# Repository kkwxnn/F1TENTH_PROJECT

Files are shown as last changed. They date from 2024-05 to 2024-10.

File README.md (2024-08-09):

# F1TENTH: Autonomous Ackermann Steering Mobile Robot

https://github.com/user-attachments/assets/e7468762-8f40-447a-a497-539dd0bba7ac

### Obstacle Avoidance
https://github.com/user-attachments/assets/739e911e-5323-4bcc-a1b8-9813c5cff750

## Table of Contents
1. [Hardware](#1-hardware)
   - [1.1 Chassis](#11-chassis)
   - [1.2 Laser Sensor](#12-laser-sensor)
   - [1.3 Sensors](#13-sensors)
   - [1.4 Microcontroller](#14-microcontroller)
   - [1.5 Processor](#15-processor)
   - [1.6 Motor](#16-motor)
   - [1.7 Motor Driver](#17-motor-driver)

2. [Electrical & Firmware](#2-electrical--firmware)
   - [2.1 Electrical Components](#21-electrical-components)
   - [2.2 F1TENTH PCB Schematic](#22-f1tenth-pcb-schematic)
   - [2.3 Firmware](#23-firmware)

3. [High-Level](#3-high-level)
   - [3.1 Docker Setup](#31-docker-setup)
     - [3.1.1 Prerequisites](#311-prerequisites)
     - [3.1.2 Services](#312-services)
     - [3.1.3 Usage](#313-usage)
   - [3.2 TF](#32-tf)
     - [3.2.1 Coordinate Frame Transformations](#321-coordinate-frame-transformations)
     - [3.2.2 Visualization](#322-visualization)
   - [3.3 Localization](#33-localization)
     - [3.3.1 Prepare Sensor for Localization](#331-prepare-sensor-for-localization)
     - [3.3.2 Wheel Odometry (Yawrate Odometry)](#332-wheel-odometry-yawrate-odometry)
   - [3.4 Mapping & Localization by Slam Toolbox](#34-mapping--localization-by-slam-toolbox)
     - [3.4.1 Creating Map](#341-creating-map)
     - [3.4.2 Creating Keepout Zone](#342-creating-keepout-zone)
   - [3.5 Navigation (Nav2)](#35-navigation-nav2)
     - [3.5.1 Costmap](#351-costmap)

4. [Usage](#4-usage)
   - [4.1 Run ydlidar_launch.py](#41-run-ydlidar_launchpy)
   - [4.2 Run robot_bridge.launch](#42-run-robot_bridgelaunch)
   - [4.3 Teleoperation](#43-teleoperation)
   - [4.4 Viapoint Generator](#44-viapoint-generator)
     - [4.4.1 Selecting Point from Map](#441-selecting-point-from-map)
       
## 1. Hardware
<div align="center">
  f1tenth pic
</div>

### 1.1. Chassis
- [TAMIYA 58720 1/10 R/C 4WD TT-02 Type-SRX Chassis Kit](https://www.tamiyausa.com/shop/110-4wd-shaft-drive-road-tt/rc-tt-02-type-srx-chassis-kit/)
  
### 1.2. Laser Sensor
- [YDLIDAR T-mini Pro](https://www.ydlidar.com/products/view/22.html)

### 1.3. Sensors
- 9-DOF Absolute Orientation IMU Fusion Breakout - BNO055
- [Optical Tracking Odometry Sensor - PAA5160E1](https://www.sparkfun.com/products/24904) (Optional)
  
### 1.4. Microcontroller
- [STM32L432KC](https://www.st.com/en/evaluation-tools/nucleo-l432kc.html)

### 1.5. Processor
- [Raspberry Pi 5 Computer with 8GB RAM](https://www.raspberrypi.com/products/raspberry-pi-5/)
  
### 1.6. Motor
- [TAMIYA 54612 BRUSHLESS MOTOR 02 Sensored 15.5T 2300KV](https://www.tamiya.com/english/products/54612/index.html) (For main drive motor)
- [MG996R Servo Tower Pro](https://www.towerpro.com.tw/product/mg996r/) (For steering motor)
  
### 1.7. Motor Driver
- [TAMIYA 45070 TBLE-04SR BRUSHLESS ELECTRONIC SPEED CONTROLLER](https://www.tamiya.com/english/products/45070/index.html)

 > [!TIP]
 > **High Point Setup**
 > 1. Press and hold down Set button. LED will light up in the order Red → Green → Orange → Red. Release the Set button when the LED is lit up Red, and it will start to flash Red.
 > 2. Apply full throttle and press Set button once. If procedure has been performed correctly, LED will start to double flash Red.
 > 3. Apply full brake and press Set button once. If procedure has been performed correctly, LED will turn off.
 > 
 > [Tamiya Brushless ESC 04SR Manual](https://www.tamiyausa.com/media/files/45070ml-1206-1b53.pdf)

## 2. Electrical & Firmware
### 2.1. Electrical Components
- Step down DC-DC 4.5-30V to 0.8-30V 12A
- HW-683 Module

### 2.2. F1TENTH PCB Schematic
View full PCB schematic in EasyEDA within [this link](https://u.easyeda.com/join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)

<div align="center">
  Schematic_F1TENTH_V4_2024-07-18
  PCB_F1TENTH_V4_2024-07-18
</div>

### 2.3. Firmware

Process for Setup Low-Level is within [this link](https://github.com/tanakon-apit/F1TENTH_PROJECT.git)

## 3. High-Level 

### 3.1. Docker Setup

Instructions for using the provided `docker-compose.yml` file to set up and run a micro-ROS agent and a ROS 2 desktop environment with VNC access.

#### 3.1.1. Prerequisites
- [Install Docker](https://www.digitalocean.com/community/tutorials/how-to-install-and-use-docker-on-ubuntu-22-04)
- Install Docker Compose

#### 3.1.2. Services
**1. micro_ros_agent** runs a micro-ROS agent that connects to a serial device.

- Image: `microros/micro-ros-agent:humble`
- Container Name: `micro-ros-agent`
- Network Mode: `host`
- Command: `serial --dev /dev/ttyACM0 --baudrate 2000000`
- Devices:
    - `/dev/ttyACM0:/dev/ttyACM0`
- Restart Policy: `unless-stopped`

**2. desktop_ros2** runs a ROS 2 desktop environment with VNC access, allowing you to interact with ROS 2 via a web browser. [Reference](https://github.com/Tiryoh/docker-ros2-desktop-vnc.git)

- Image: `kkwxnn/f1tenth-vnc:humble`
- Container Name: `desktop_ros2`
- Security Options:
    - `seccomp=unconfined`
- Shared Memory Size: `512m`
- IPC Mode: `host`
- Ports: `6080:80` (Maps port 6080 on your host to port 80 in the container)
- Volumes: 
    - `~/F1TENTH_PROJECT/ros2_ws:/f1tenth_ws:rw` (Mounts your local workspace to the container)
    - `/dev:/dev` (Mounts the host's /dev directory to the container)
- Devices:
    - `/dev/ttyUSB0:/dev/ttyUSB0`
- Restart Policy: `unless-stopped`

#### 3.1.3. Usage
**1. Start the Services**

To start the services defined in the docker-compose.yml file, navigate to the directory containing the file and run:

```
docker compose up 
```
**2. Connect Raspberry Pi via SSH**

- Finding IP Address of wlan0 (wifi)
```
ifconfig
```
- Connect Raspberry Pi your computer via SSH
```
ssh -L 6080:localhost:6080 [username]@[inet addr] 
```
For example: ```ssh -L 6080:localhost:6080 pi@192.168.0.152```

**3. Access the ROS 2 Desktop**

Open a web browser and navigate to http://127.0.0.1:6080/ to access the ROS 2 desktop environment via VNC.

**4. Reset the services**
```ctrl+c```

> [!WARNING]
> If you are unable to connect to the ROS 2 desktop via noVNC, follow these steps:
> 
> - Remove the container
> ```
> docker compose down
> ```
> 
> - Start the services again
> ```
> docker compose up 
> ```
> 
> - Reinstall the libraries and dependencies
> ```
> sudo apt update && rosdep update
> rosdep install --from-paths src
> ```

> [!TIP]
> To avoid the need to reinstall libraries and dependencies, you can push your Docker image to Docker Hub. Follow these steps to do.
> 
> Don't forget to **logout of ubuntu in docker** and **stop the docker** before pushing the image.
> ```
> docker stop [container_id_or_name]
> ```
> - Log in to Docker Hub
>
> ```
> docker login
> ```
> - Commit the container
> ```
> docker commit [container_id_or_name] your-username/your-repository:tag
> ```
>
> For example: ```docker commit 1a2b3c4d5e6f your-username/my-app:latest```
> 
> - Tag Your Docker Image
> ```
> docker tag your-image:tag your-username/your-repository:tag
> ```
> For example: ```docker tag my-app:latest your-username/my-app:latest```
>
> - Push the Image to Docker Hub
>
> ```
> docker push your-username/your-repository:tag
> ```
> For example: ```docker push your-username/my-app:latest```

> [!CAUTION]
> In the event that **Docker crashes** and **Docker images and containers disappear**, but **noVNC is still running**, you will need to repeat the `docker compose up` steps and clear the running noVNC instance by following these steps.
>
> - Identify Running noVNC 
> ```
> ps aux | grep localhost
> ```
> - Terminate the noVNC 
> ```
> sudo kill [Process IDs]
> ```
> For example: ```sudo kill 3322```
> - Restart Docker
> ```
> sudo service docker restart
> ```
> or
> ```
> sudo systemctl restart docker
> ```

### 3.2. TF

<div align="center">
  <img src="https://github.com/user-attachments/assets/e0d1709a-a66c-4ba6-8a19-d0308fb0f621" alt="Robot_Description" width="600">
</div>

#### 3.2.1. Coordinate Frame Transformations

#### 3.2.1.1. base_footprint -> **base_link**

- This transform represents the static relationship between the center of the robot base (`base_footprint`) and the floor (`base_link`).

#### 3.2.1.2. base_link -> **imu**

- This transform describes the static relationship between the robot's base (`base_link`) and the IMU (Inertial Measurement Unit) sensor (`imu`).

#### 3.2.1.3. base_link -> **left_wheel**

- This transform defines the revolute relationship between the robot's base (`base_link`) and the left wheel (`left_wheel`).

#### 3.2.1.4. base_link -> **right_wheel**

- This transform defines the revolute relationship between the robot's base (`base_link`) and the right wheel (`right_wheel`).

#### 3.2.1.5. base_link -> **steer**

- This transform defines the static relationship between the robot's base (`base_link`) and the lidar sensor (`steer`).

#### 3.2.1.6. imu -> **laser_frame**

- This transform defines the static relationship between imu (`imu`) and the lidar sensor (`laser_frame`). 

#### 3.2.1.7. base_link -> **optical_odom**

- This transform defines the static relationship between the robot's base (`base_link`) and the Optical Tracking Odometry Sensor (`optical_odom`).

#### 3.2.2. Visualization

#### 3.2.2.1. Launch Robot Description

- Run the following command to launch the robot's description

```
ros2 launch robot_bridge robot_bridge.launch.py 
```
#### 3.2.2.2. View Transformations

- Execute the following command to watch the relationships between the robot's transformations

```
ros2 run tf2_tools view_frames
```

This command opens a graphical interface displaying the relationships between different frames. The provided link shows an example image capturing these transformations:

<div align="center">
  <img src="https://github.com/user-attachments/assets/61efbc9a-44b0-4ba7-a626-1a6dac1811cc" alt="TF_frames" width="900">
</div>

### 3.3. Localization

#### 3.3.1. Prepare sensor for Localization

1) IMU Sensor

    - Calibration sensor

        To calibrate IMU sensor you need to use STM32Cubeide this calibration file is set up for `STM32L432KC` follow this link to low-level github (branch: CalibrateIMU) [[link]](https://github.com/tanakon-apit/F1TENTH_PROJECT/tree/CalibrateIMU)

        Open up the project `BNO_Calibrate` in STM32Cubeide.

        Monitor the `Calibrated` value in the debugger's live expressions to track calibration progress (Accel, Gyro, Magneto).

        - `Magnetometer`: Hold the sensor parallel to the ground and move it in a figure 8 pattern.
        - `Accelerometer`: Place the BNO055 sensor in these six stable positions for a few seconds each.
        - `Gyroscope`: Place the sensor in any stable position for a few seconds.

        After successful calibration, record the BNO offsets from the bno variable in the debugger's live expressions.

        Change branch from `CalibrateIMU` to `Main`, Within the project, navigate to the file `Mobile_Config.h` located in the `Config/inc` directory. Write the BNO offsets from recorded. Then upload code into `STM32L432KC`.

    - Find Offset & Covariance sensor

        - Using `Calibration Node` to find offset and covariance of imu.
            - Collect 10,000 sensor raw data && Save offset and covariance data in YAML file.

            ```
            ros2 run calibration_gen cal_node.py
            ```

            - Copy the information from `f1tenth_ws/install/calibration_gen/share/calibration_gen/config/sensor_calibration.yaml` and paste in `f1tenth_ws/src/calibration_gen/config/sensor_calibration.yaml` 

        - Eliminating noise at stationary state by cutting threshold this will be done by `mcu_bridge` Node.
        
            - `threshold`: 2 x std. x 3.89 (Modeling Noise as Normal Distribution)

    - Verification sensor 

        - Testing Absolute Orientation from imu

            Testing Condition:

            - Turn 90, 180, 360 Degree (R/L)
            - Turn Right then Left 90 Degree

            https://github.com/user-attachments/assets/508171c0-2647-4e11-aa7b-1ab644b267a2

        **The IMU will shift of ±6 degrees each time it completes a full 360-degree rotation.**

2) Laser Sensor 

**Install YDLIDAR ROS2 Driver** [Reference](https://github.com/YDLIDAR/ydlidar_ros2_driver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)

- Clone ydlidar_ros2_driver package for github in `src` folder

```
git clone https://github.com/YDLIDAR/ydlidar_ros2_driver.git 
```
- Clone YDLidar-SDK package for github in `src` folder

```
git clone https://github.com/YDLIDAR/YDLidar-SDK.git
```

- Build & Install [Reference](https://github.com/YDLIDAR/YDLidar-SDK/blob/master/doc/howto/how_to_build_and_install.md)

```
cd YDLidar-SDK
mkdir build
cd build
cmake ..
make
sudo make install
```

- Build ydlidar_ros2_driver package

```
cd [your_workspace]
colcon build --symlink-install
```

#### Usage: Laser Sensor

1. Connect LiDAR
```
ros2 launch ydlidar_ros2_driver ydlidar_launch.py
```

2. Visualization in RVIZ
```
ros2 launch ydlidar_ros2_driver ydlidar_launch_view.py 
```

<div align="center">
  <img src="https://github.com/user-attachments/assets/7b7f3aa2-0fd3-449e-af10-5252123fc776" alt="Lidar" width="550">
</div>

#### 3.3.2. Wheel Odometry (Yawrate Odometry)

**State Equation**

$$ 
\begin{bmatrix}
x_k \\
y_k \\
\theta_k \\
\beta_k \\
v_k
\end{bmatrix}
=\
\begin{bmatrix}
x_{k-1} + v_{k-1} \cdot \Delta t \cdot \cos(\beta_{k-1} + \theta_k) \\
y_{k-1} + v_{k-1} \cdot \Delta t \cdot \sin(\beta_{k-1} + \theta_k) \\
\theta_k \\
0 \\
\text{motor speed} \cdot \text{gear ratio} \cdot r
\end{bmatrix} 
$$

where:
- $x_k$ and $y_k$ are the vehicle's position coordinates at time step $k$.
- $\theta_k$ is the vehicle's orientation (heading angle) at time step $k$.
- $\beta_k$ is the vehicle's slip angle at time step $k$.
- $v_k$ is the vehicle's velocity at time step $k$.

**Verification**

A ceiling-mounted camera in the laboratory serves as a ground truth reference for verifying the yaw rate odometry calculations. These calculations are derived from data obtained from both a hall sensor and an IMU sensor.

<div align="center">
  <img src="https://github.com/user-attachments/assets/81ab683f-14e1-4523-b5d4-ec480f5cf7b3" alt="Camera" width="550">
</div>

#### Experiment 1: Circular Path for 5 Rounds at speed 0.5 m/s

| Position | Odometry Final Position (m) | Camera Final Position (m) | Final Position Error (m) | RMSE (m) |
|----------|-----------------------------|---------------------------|--------------------------|----------|
| X (Y axis of the car frame) | 3.71 | 3.59 | 0.12 | 0.16 |
| Y (X axis of the car frame) | 4.78 | 5.13 | -0.35 | 0.21 |

<div align="center">
  <img src="https://github.com/user-attachments/assets/8b13dcbc-7981-4dc6-95a7-168b0b864c3f" alt="Circular Path" width="550">
</div>

#### Experiment 2: Path Around the Object at speed 0.5 m/s

| Position | Odometry Final Position (m) | Camera Final Position (m) | Final Position Error (m) | RMSE (m) |
|----------|-----------------------------|---------------------------|--------------------------|----------|
| X (Y axis of the car frame) | 2.54 | 2.57 | -0.03 | 0.06 |
| Y (X axis of the car frame) | -1.20 | -1.00 | -0.20 | 0.11 |

<div align="center">
  <img src="https://github.com/user-attachments/assets/464721fc-f9a7-4065-8367-265360b34701" alt="Obj Path" width="550">
</div>

### 3.4. Mapping & Localization by Slam toolbox

#### 3.4.1. Creating Map

To create a map, run the following command:

```bash
ros2 launch robot_bridge caver_mapping.launch.py
```

Once RVIZ has fully loaded, you need to launch teleop to control the robot for creating map.

```bash
ros2 run teleop_twist_keyboard teleop_twist_keyboard
```

After you have created a map, you can save it using the following command:

```bash
ros2 launch robot_bridge vmegarover_save_map.launch.py
```

Two file will be saved where you ran the command in the folder maps. The `.pgm` file is the map image and the `.yaml` file is the map metadata.

You can change the map name by rename the `.pgm` and `.yaml` file. You also need to foward in to `.yaml` file and change the name to the same name as `.pgm` file

You can change the map name by renaming both the `.pgm` and `.yaml` files. Additionally, you need to open the `.yaml` file and modify the name within it to match the new `.pgm` file name.

Then, copy both files and paste into the `maps` folder located within the `src` folder.

To use a specific map, you'll need to modify the map file name within the Python launch script. 

Running the following command will open the Python launch script in Visual Studio Code:

```bash
code /src/robot_bridge/lauch/robot_bridge.launch.py
```
Finally, you will obtain a map similar to the one shown below.

<div align="center">
  Map
</div>

#### 3.4.2. Creating Keepout zone

To create a keepout zone, make a copy of both the `.pgm` and `.yaml` files and rename them to `keepout_<map_name>.pgm` and `keepout_<map_name>.yaml` respectively.

Open the `keepout_<map_name>.yaml` file and change the `image` parameter to `keepout_<map_name>.pgm`.

Using image editing software, such as GIMP, draw the area you want to keepout in black. The rest of the image is left as is.

<div align="center">
  Keepout
</div>

### 3.5. Navigation (Nav2)

#### 3.5.1. Costmap

Environment representation used for planning and control. Combines sensor data (depth, AI, semantics) into a grid, assigning costs to cells. Higher costs indicate obstacles or risky areas. [Reference](https://docs.nav2.org/configuration/packages/configuring-costmaps.html)

-  Critical Costmap2D ROS Parameters 
    - `Footprint`

        polygon updated over time due to change of robot's state (base_footprint). If this parameter is set, `isPathValid` will do full collision checking.
        - `Robot_radius`: If footprint coordinates not provided. If this parameter is set, `isPathValid` will do circular collision checking.
    - `plugin`: 
        - `StaticLayer`: 
        
            Static obstacles on the planning space.
            - `footprint_clearing_enabled`: Clear any occupied cells under robot footprint.

        - `ObstacleLayer`:

            Costmap layeruses that use 2D raycasting for 2D lidars, depth, or other sensors. Manages the planning space by the parameters specified
            
            - `obstacle_max_range` / `obstacle_min_range`:
            Maximum, Minimum range to mark obstacles in costmap.
            - `raytrace_max_range` / `raytrace_min_range`
        - `InflationLayer`:

            This layer places an exponential decay functions around obstacles to increase cost to traverse near collision.

            - `inflation_radius`:
            Radius to inflate costmap around lethal obstacles.
            - `cost_scaling_factor`: Exponential decay factor across inflation radius.

-  Costmap2D ROS Parameters tunning guide

    - `Footprint`: For precise navigation in tight spaces, use a detailed robot footprint. In open areas, a simple `Robot_radius` can optimize performance (Collision detection computation time).

    - `obstacle_max_range`-`obstacle_min_range` / `raytrace_max_range`-`raytrace_min_range`: A longer sensor range enhances obstacle detection, improving path planning and collision avoidance. Conversely, a shorter range can expedite computation but limits obstacle awareness.

    - Increasing both `inflation_radius` and `cost_scaling_factor` amplifies the cost area around obstacles. To achieve a stronger cost effect, prioritize increasing `cost_scaling_factor` first (more `cost_scaling_factor` will decrease cost area).

<div align="center">
  costmap_lowcost
  costmap_highcost
  
  *`inflation_radius`: low [0.275], high [2.0]*
  
  *`cost_scaling_factor`: low [15.0], high [16.5]*
</div>

 - Example of the nav2 configuration can be found at the following [here](https://github.com/kkwxnn/F1TENTH_PROJECT/blob/humble/f1tenth_ws/src/robot_bridge/config/navigation_param.yaml).

#### 3.5.2. Planner

`Smac Hybrid-A* Planner`

Creates various A* planners for different robots (cars, legged). Supports Hybrid-A* for complex maneuvers (kinematically feasible and support reversing). [Reference](https://docs.nav2.org/configuration/packages/configuring-smac-planner.html)

-  Critical Planner ROS Parameters

    - `allow_unknown`: Allow traversing/search in unknown space.
    - `motion_model_for_search`: Motion model (`Dubin`, `Redds-Shepp`). 
    - `minimum_turning_radius`: Minimum turning radius in meters of vehicle.
    - `reverse_penalty`: Heuristic penalty to apply to SE2 node if searching in reverse direction. Only used in `REEDS_SHEPP` motion model.
    - `non_straight_penalty`: Heuristic penalty to apply to SE2 node if searching in non-straight direction.
    - `cost_penalty`: Heuristic penalty to apply to SE2 node for cost at pose. Allows Hybrid-A* to be cost aware.

 - Example of the nav2 configuration can be found at the following [here](https://github.com/kkwxnn/F1TENTH_PROJECT/blob/humble/f1tenth_ws/src/robot_bridge/config/navigation_param.yaml).

 - Planner ROS Parameters tunning guide: 

    - Reccomend `Dubin` if the robot has not recommend to reverse.

    - Using the exact `minimum_turning_radius` aids robot to follow, while a slightly reduced value can smooth path planning.
    <div align="center">
      low_curvature
      high_curvature
      
      *`minimum_turning_radius`: low [0.73], high [1.20]*
    </div>

    - Increasing the `non_straight_penalty` heuristic promotes straighter paths in path planning.

    <div align="center">
      Non_straight_penalty
      straight_penalty
      
      *`non_straight_penalty`: low [1.2], high [2.0]*
    </div>

    - A higher `cost_penalty` incentivizes the planner to avoid high-cost regions, typically obstacles.

#### 3.5.3. Controller

`Regulated Pure Pursuit`

Adaptive speed based on path curvature for safer industrial robot navigation. Prevents overshoot in corners. [Reference](https://docs.nav2.org/configuration/packages/configuring-regulated-pp.html)

If you use the Regulated Pure Pursuit Controller algorithm or software from this repository, please cite this work in your papers:
Macenski, S. Singh, F. Martin, J. Gines, [Regulated Pure Pursuit for Robot Path Tracking](https://arxiv.org/abs/2305.20026). Autonomous Robots, 2023.

- Controller ROS Parameters tunning

    - `desired_linear_vel`: The desired maximum linear velocity (m/s) to use.

    - `use_velocity_scaled_lookahead_dist` is `false`.
        - `lookahead_dist`: The lookahead distance (m) to use to find the lookahead point when 

    - `use_velocity_scaled_lookahead_dist` is `true`.
        - `min_lookahead_dist` / `max_lookahead_dist`: The minimum / maximum lookahead distance (m) threshold when 

        - `lookahead_time`: The time (s) to project the velocity. Also known as the lookahead gain.

    - `use_cost_regulated_linear_velocity_scaling`: Whether to use the regulated features for proximity to obstacles (e.g. slow in close proximity to obstacles).

    - `use_regulated_linear_velocity_scaling`: use the regulated features for path curvature (e.g. slow on high curvature paths).

        - `regulated_linear_scaling_min_radius`: The turning radius (m) for which the regulation features are triggered.

    - `regulated_linear_scaling_min_speed`: To ensure process is still achievable even in high cost spaces with high curvature.

    - `use_fixed_curvature_lookahead`: Use a fixed lookahead distance to compute curvature from.

        - `curvature_lookahead_dist`: Distance to look ahead on the path to detect curvature.

- Controller ROS Parameters tunning guide:

    - `Regulated Pure Pursuit` enhances curve following by adjusting speed through the `regulated_linear_scaling_min_radius` parameter. Higher values reduce speed on tighter curves.

    - Enabling `use_cost_regulated_linear_velocity_scaling` prioritizes obstacle avoidance by reducing speed in high-cost areas.

    - If the area the robot need to traverse high-cost areas, increasing `regulated_linear_scaling_min_speed` enables the robot to traverse by maintaining a minimum velocity.

 - Example of the nav2 configuration can be found at the following [here](https://github.com/kkwxnn/F1TENTH_PROJECT/blob/humble/f1tenth_ws/src/robot_bridge/config/navigation_param.yaml).

 #### 3.5.4. AMCL

 AMCL implements the server for taking a static map and localizing the robot within it using an Adaptive Monte-Carlo Localizer. [Reference](https://docs.nav2.org/configuration/packages/configuring-amcl.html)

 -  Critical AMCL ROS Parameters 

    - Odometry
        - `alpha1`: Expected process noise in odometry’s rotation estimate from rotation.
        - `alpha2`: Expected process noise in odometry’s rotation estimate from translation.
        - `alpha3`: Expected process noise in odometry’s translation estimate from translation.
        - `alpha4`: Expected process noise in odometry’s translation estimate from rotation.
        - `pf_err`: Particle Filter population error.
        - `pf_z`: Particle filter population density. 2.33 is the 99% percentile.
    - Laser (Lidar)
        - `laser_likelihood_max_dist`: Maximum distance to do obstacle inflation on map, for use in likelihood_field model.
        - `sigma_hit`: Standard deviation for Gaussian model used in z_hit part of the model.
        - `z_hit` / `z_rand`: Mixture weight for z_hit part of model, sum of all used z weight must be 1.

- AMCL ROS Parameters tunning guide:

    - Our odometry model is more stable than the laser scan (lidar) data.

    - For a reliable odometry model, reduce expected process noise (`alpha`) and `pf_er`r, while increasing `pf_z`.

    - For unreliable lidar data, increase `z_hit` and `sigma_hit` to incoporate higher measurement noise.

 - Example of the nav2 configuration can be found at the following [here](https://github.com/kkwxnn/F1TENTH_PROJECT/blob/humble/f1tenth_ws/src/robot_bridge/config/navigation_param.yaml).

Parameters prioritize `odometry` over `lidar`.
```
lazer_z_hit = 0.9
laser_sigma_hit = 0.1
laser_z_rand = 0.5
laser_likelihood_max_dist = 4.0
kld_err = 0.01
kld_z = 0.99
odom_alpha1 = 0.005
odom_alpha2 = 0.005
odom_alpha3 = 0.005
odom_alpha4 = 0.005
```
https://github.com/user-attachments/assets/a85da535-ef96-4c38-8924-c9d862924488

Parameters prioritize `lidar` over `odometry`.
```
lazer_z_hit = 0.5
laser_sigma_hit = 0.2
laser_z_rand = 0.5
laser_likelihood_max_dist = 2.0
kld_err = 0.1
kld_z = 0.5
odom_alpha1 = 0.004
odom_alpha2 = 0.04
odom_alpha3 = 0.008
odom_alpha4 = 0.025
```

https://github.com/user-attachments/assets/7fe0a6d9-28dd-49fd-9026-d1f11126844d

 **Verification**

 #### Experiment 1: Path Around the Object at Speed 0.5 m/s

| Position | Camera Last Position (m) | TF Last Position (m) | Error Odom Last Position (m) | Error AMCL Last Position (m) | Error TF Last Position (m) | RMSE TF (m) |
|---|---|---|---|---|---|---|
| X (Y axis of the car frame) | 2.57 | 2.62 | -0.03 | 0.10 | 0.05 | 0.11 |
| Y (X axis of the car frame) | -1.00 | -1.05 | -0.20 | 0.05 | -0.05 | 0.14 |

<div align="center">
  amcl_tune0.5
</div>

#### Experiment 2: Path Around the Object at Speed 2.0 m/s

| Position | Camera Last Position (m) | TF Last Position (m) | Error Odom Last Position (m) | Error AMCL Last Position (m) | Error TF Last Position (m) | RMSE TF (m) |
|---|---|---|---|---|---|---|
| X (Y axis of the car frame) | 2.53 | 2.55 | -0.19 | 0.00 | 0.01 | 0.40 |
| Y (X axis of the car frame) | 0.69 | 0.66 | -0.18 | 0.02 | -0.03 | 0.47 |

<div align="center">
  amcl_tune2.0
</div>

## 4. Usage

To run the robot, you should first connect to Docker and then run the following terminal commands.

### 4.1. Run ydlidar_launch.py
```
ros2 launch ydlidar_ros2_driver ydlidar_launch.py 
```

### 4.2. Run robot_bridge.launch 
```
ros2 launch robot_bridge robot_bridge.launch.py
```

### 4.3. Teleoperation
```
ros2 run teleop_twist_keyboard teleop_twist_keyboard
```
[Reference](https://index.ros.org/r/teleop_twist_keyboard/)
```
This node takes keypresses from the keyboard and publishes them as Twist
messages. It works best with a US keyboard layout.
---------------------------
Moving around:
   u    i    o
   j    k    l
   m    ,    .

For Holonomic mode (strafing), hold down the shift key:
---------------------------
   U    I    O
   J    K    L
   M    <    >

t : up (+z)
b : down (-z)

anything else : stop

q/z : increase/decrease max speeds by 10%
w/x : increase/decrease only linear speed by 10%
e/c : increase/decrease only angular speed by 10%

CTRL-C to quit
```
### 4.4. viapoint generator

#### 4.4.1. Selecting point from Map

After lauch robot_bridge.launch.py

```
ros2 topic echo /clicked_point 
```

Click the `Publish Point` button, then select the desired goal point. 

Edit the goal point by modifying the `self.current_goal_pose` value (in [x, y, yaw] format) within the `navigation_param.yaml` file located in the `src/robot_bridge/config` directory.

For example: `self.current_goal_pose` = [[3.6, 0.0, np.deg2rad(0)]]

```
code src/robot_bridge/config/navigation_param.yaml
```

> [!WARNING]
> If your next goal point doesn't generate (Feedback: Reached), consider relocating it or increasing the error threshold. Path planning difficulties might be causing the issue.

After defining all goal points you can execute the Python script from Visual Studio Code or run it as a command below:

```
ros2 run robot_bridge via_points_generator.py
```

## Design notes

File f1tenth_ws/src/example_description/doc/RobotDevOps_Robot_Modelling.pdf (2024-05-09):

# NOTICE OF CONFIDENTIALITY AND USE RESTRICTIONS

This PowerPoint presentation, including all of its contents, is the intellectual property of Pi Thanacha Choopojcharoen. It has been exclusively designed and created for the "RobotDevOps" class.
Authorized Users:
If you are currently enrolled in or have previously taken the "RobotDevOps" class and are in possession of this presentation, you acknowledge and agree to the following:
a) This presentation is provided to you solely for your personal reference and educational use related to the "RobotDevOps" class.
b) You do not have the right to reproduce, distribute, share, or disseminate this presentation, in whole or in part, to any third parties, especially those who have not registered for the "RobotDevOps" class, unless explicitly authorized by Pi Thanacha Choopojcharoen.
c) Any unauthorized use or distribution of this presentation will result in legal action and potential academic sanctions. Unauthorized Possession:
a) If you have come into possession of this presentation but have not registered for the "RobotDevOps" class: You must delete this presentation immediately.
b) You do not have any rights to view, use, copy, or distribute this presentation.
c) Any unauthorized retention or use will result in legal action.

Your respect for intellectual property rights ensures a fair academic and professional environment for all. Violation of these terms is a breach of trust and may have serious legal and academic consequences.

For FRA502 only

# RBE502: RobotDevOps

# Robot Modelling

by

## Pi Thanacha Choopojcharoen

Agenda - purpose - interface - coordinate frame - visualization - URDF - XACRO - Frame prefix

# Exercise

# Exercise

Exercise

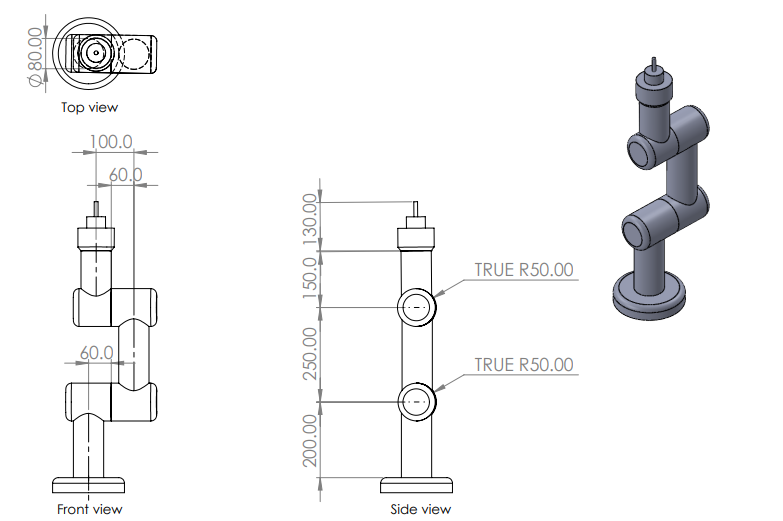
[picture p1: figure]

# Exercise

Exercise

F1

Fbase

F2

F3

Fe

# Exercise

Exercise

F1

Fbase

F2

F3

Fe

Create the robot “kinematics” model and visualize it in rviz.
[Optional] It should take namespace as well.

# Example Repo- Branch: robot-modelling-exercise

## https://github.com/kittinook/FRA501/tree/robot-modelling-exercise

## Download & add “example_description” to the “src” directory of your

workspace. Then build these packages.

## Follow the instruction on README.md

Exercise

# Existing Packages

# Type of ROS2 Packages

10 Existing Packages

Binary Package | Source Package

# Type of ROS2 Packages

11 Existing Packages

Binary Package | Source Package

Installing aruco_msgs package:

>> sudo apt install ros-humble-aruco-msgs

All underscore must be changed to hyphen.

# Type of ROS2 Packages

12 Existing Packages

Binary Package | Source Package

Installing aruco_msgs package:

>> sudo apt install ros-humble-aruco-msgs

Clone the package to “src” folder of the workspace and treat it as any other custom package.

# What binary packages are available?

13 Existing Packages

https://index.ros.org/packages

>> apt search ros-humble-

# Available & Installed Packages

14 Existing Packages

Check package’s existence in the binary package index

>> apt list ros-humble-aruco*

Check installed packages on the computer

>> apt list --installed ros-humble-aruco*

“aruco*” means any package with the name starts with “aruco” and ends with anything.

# Package Dependencies

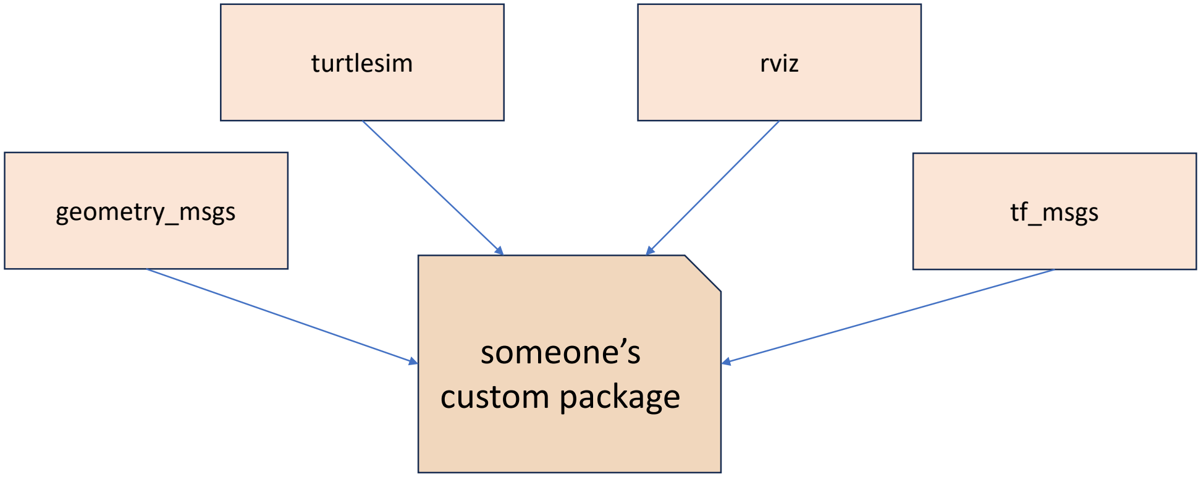
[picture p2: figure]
someone’s custom package; geometry_msgs; turtlesim; rviz; tf_msgs

15 Existing Packages

# Package Dependencies

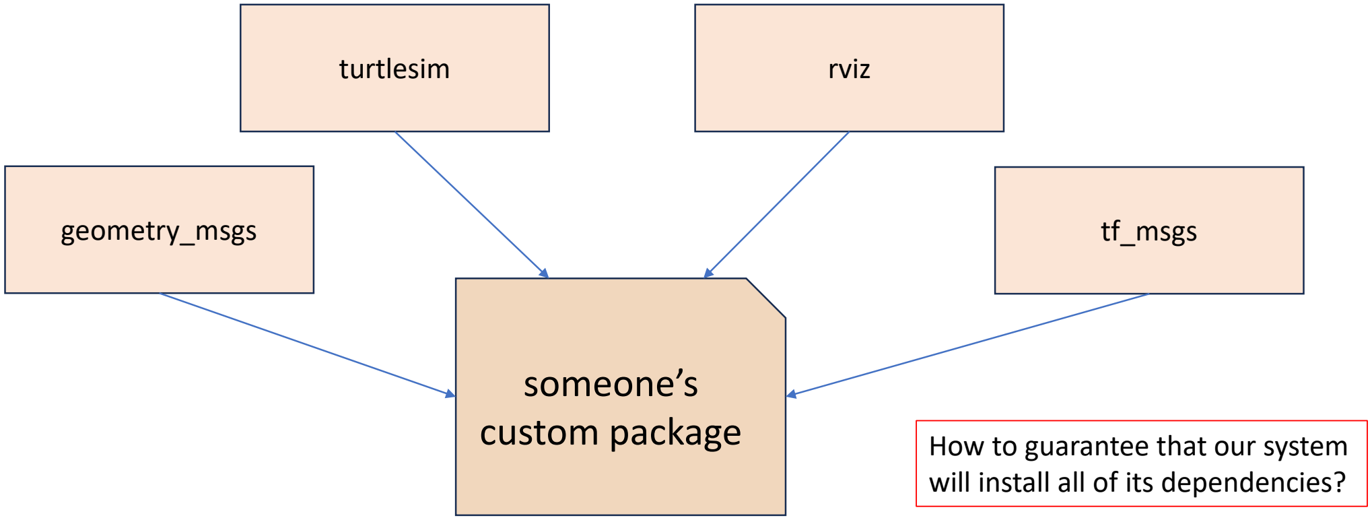
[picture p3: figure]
someone’s custom package; geometry_msgs; turtlesim; rviz; tf_msgs; How to guarantee that our system will install all of its dependencies?

16 Existing Packages

# Package Dependencies

17 Existing Packages

# Package Dependencies

18 Existing Packages

# 80 % Accurate

# Setting Package Dependencies

19 Existing Packages

In “package.xml” of your custom package, add <depends> tags for each binary package.

<depend> geometry_msgs </depend>
<depend> turtlesim </depend>

https://docs.ros.org/en/humble/Tutorials/Intermediate/Rosdep.html

# Installing Package Dependencies

20 Existing Packages

Run the following command to install the dependency of everything in the “src” folder of your workspace.

>> rosdep install --from-paths [path to your src]/src -y --ignore-src

https://docs.ros.org/en/humble/Tutorials/Intermediate/Rosdep.html

# Today’s packages

21 Existing Packages

## Additional packages:

## ros-humble-tf2-tools ros-humble-xacro ros-humble-joint-state-publisher-gui

## >> sudo apt install ros-humble-[package name]

https://docs.ros.org/en/humble/Tutorials/Intermediate/Rosdep.html

# Robot Modelling

# Questions regarding “Robot Modelling”

23 Robot Modelling

## What is “Robot Modelling”? Why do we need “Robot Modelling”? When do we need “Robot Modelling”? Who models robots? Who need “Robot Modelling”? Where do we do “Robot Modelling”? How do we model robots?

# What is Robot Modelling?

Robot Modelling

# What is Robot Modelling?

Robot Modelling

# What is Robot Modelling?

Concepts

Vague, Uncertain,
Some ideas

Robot Modelling

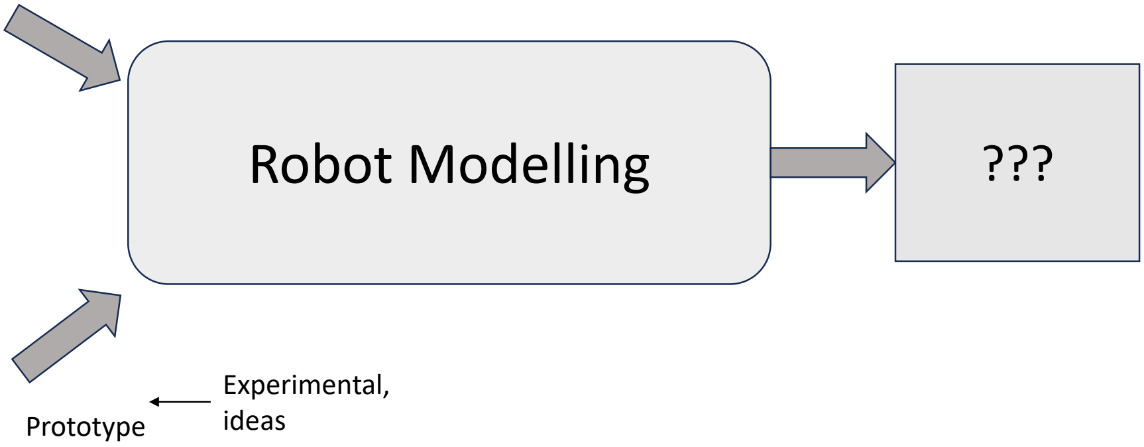
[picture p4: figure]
Robot Modelling; Prototype; Experimental, ideas

# What is Robot Modelling?

Concepts

Robot Modelling

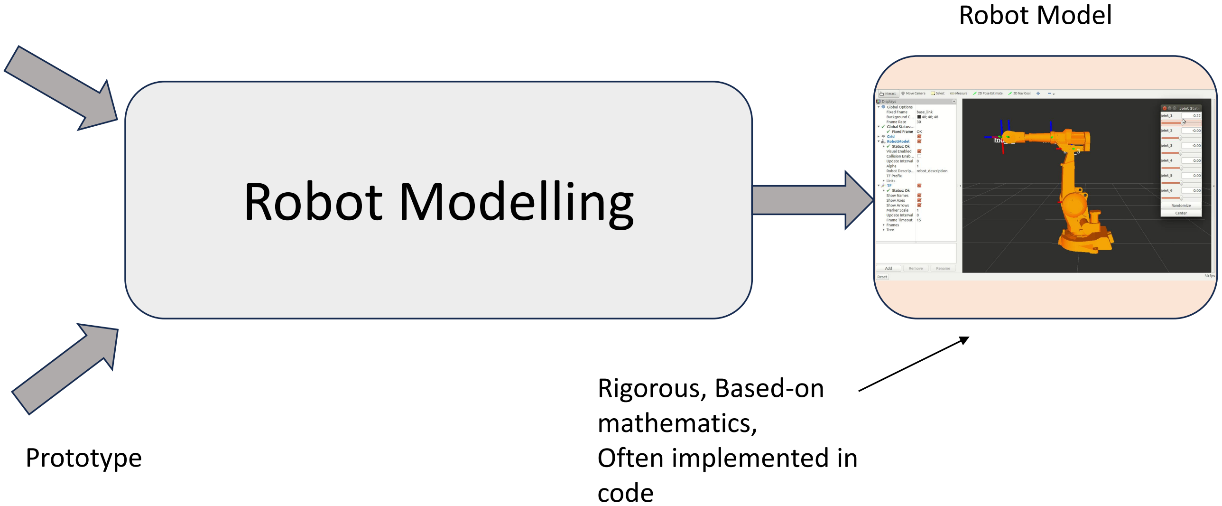
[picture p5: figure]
Robot Modelling; Prototype; Robot Model; Rigorous, Based-on mathematics, Often implemented in code

# What are robot models? And why do we need them ?

Robot Modelling

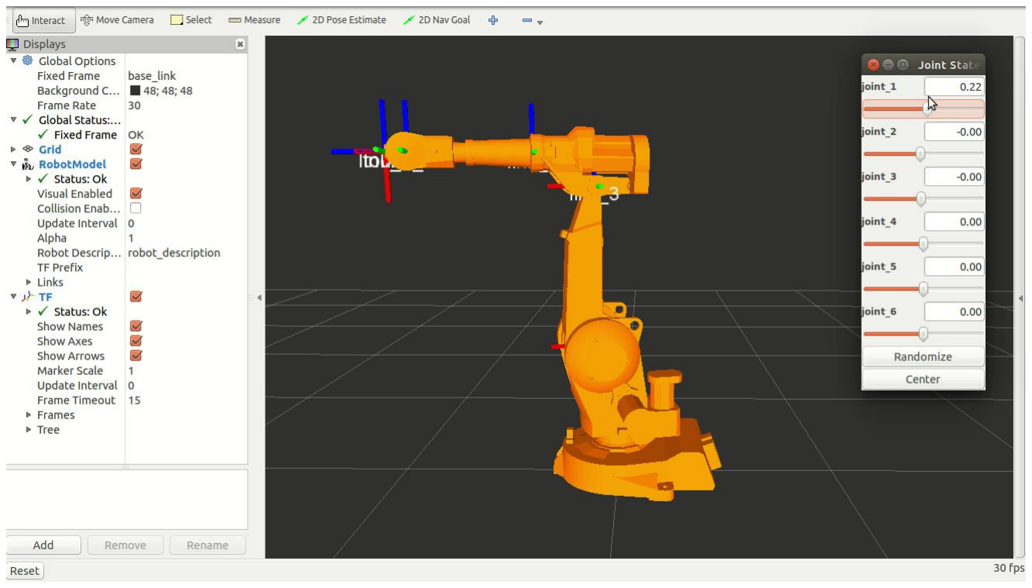
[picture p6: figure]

# What is it that the model can do, but the concept or a prototype cannot?

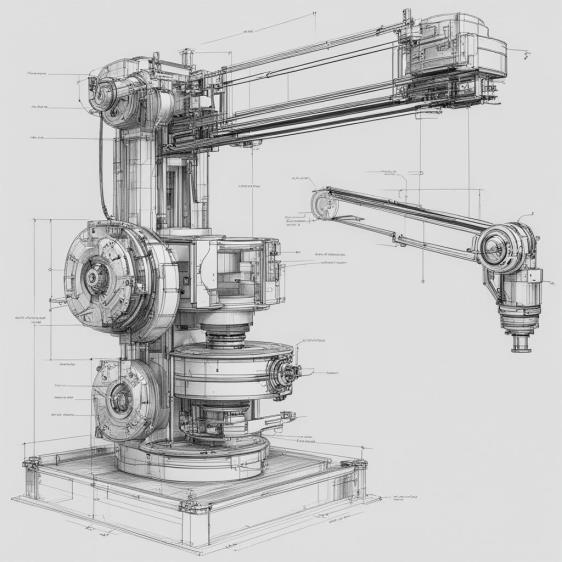
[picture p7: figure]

Robot Modelling

# Why?

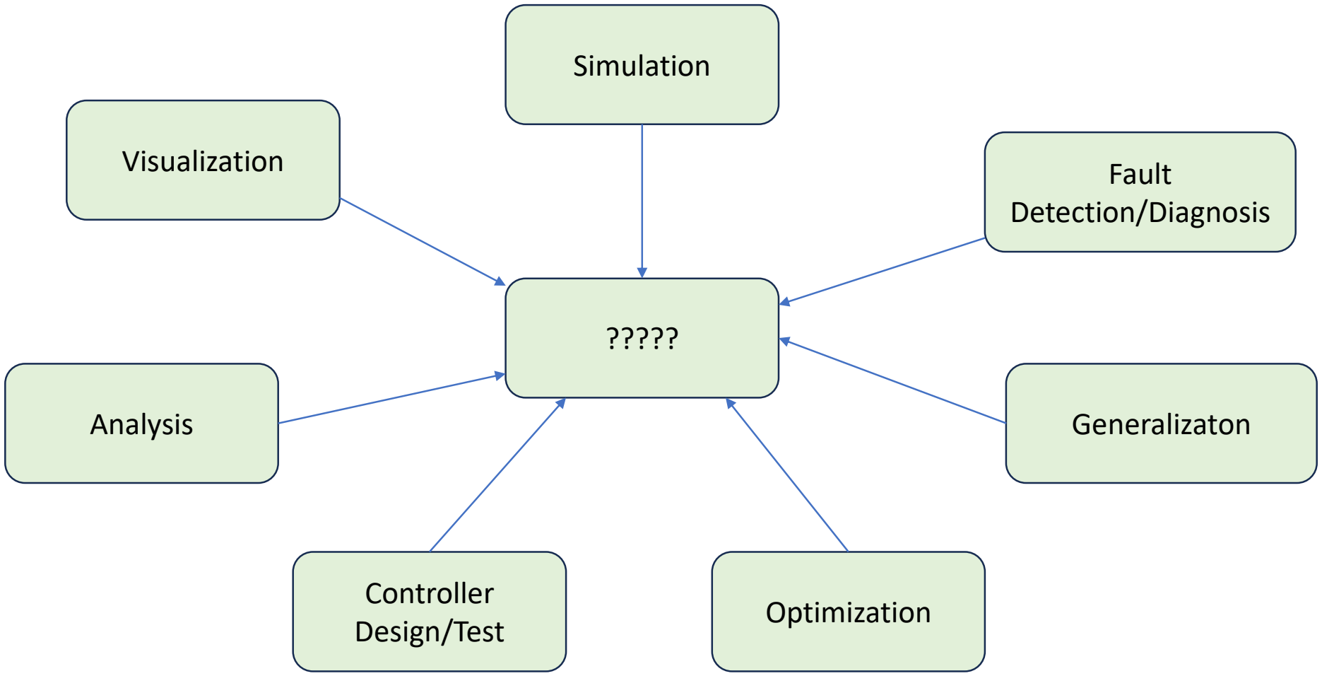
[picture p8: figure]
Simulation; Visualization; Analysis; Controller; Design/Test; Optimization; Fault Detection/Diagnosis; Generalizaton

Robot Modelling

# Why?

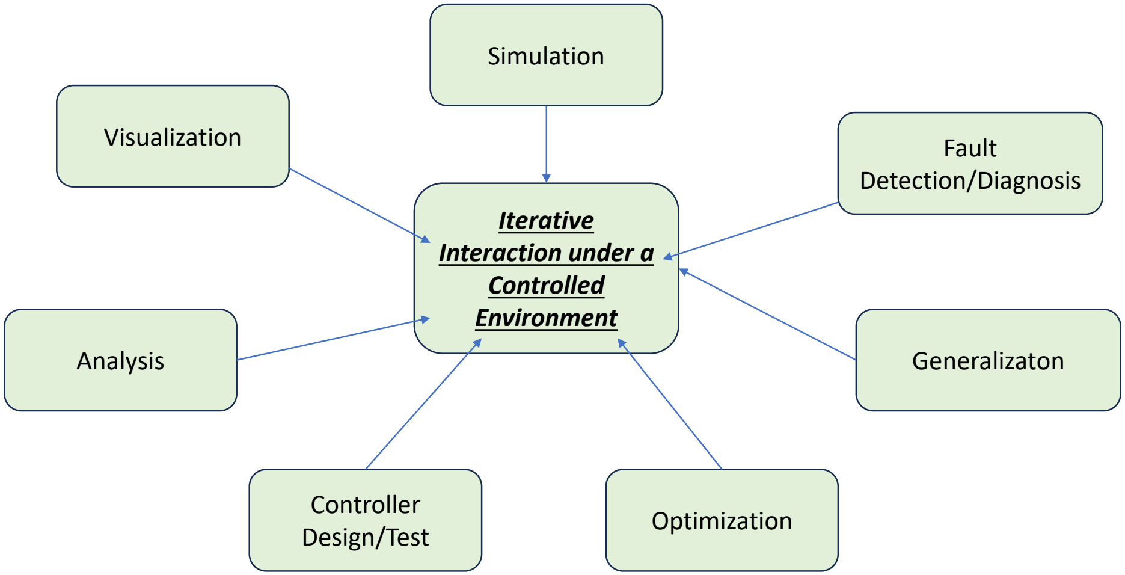
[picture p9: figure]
Simulation; Visualization; Analysis; Controller; Design/Test; Optimization; Fault Detection/Diagnosis; Generalizaton; Iterative Interaction under a Controlled Environment

Robot Modelling

## When do we need to “Robot Modelling”?

Robot Modelling

When the user requires “Iterative Interaction under a Controlled Environment”.

# What is a “robot model”?

Robot Modelling

We must identify these interfaces before “shaping” our robot model.

# Interface for a Robot Model

# What do you want from the model?

Robot Modelling

# What do you want from the “interaction”?

Robot Modelling

- Observe the position of the end-effector - Observe how fast something is going - Measure the distance travelled - Measure the actuated torque at certain revolute joints - Measure reaction force between the contact point and the ground - Obtain an ideal sensor measurement from the model - Observe any collision between the robot and the obstacle

# What do you want from the “interaction”?

Robot Modelling

- Observe the position of the end-effector - Observe how fast something is going - Measure the distance travelled - Measure the actuated torque at certain revolute joints - Measure reaction force between the contact point and the ground - Obtain an ideal sensor measurement from the model - Observe any collision between the robot and the obstacle

# Physical Quantities/Variables

Robot Modelling

Motion | Wrench
- Pose
- Joint
- Orientation
- Position
- Velocity
- Joint
- Angular
- Linear
- Acceleration
- Joint
- Angular
- Linear
- Actuator Effort
- Moment
- Force

# What can you do to the “interaction”?

Robot Modelling

# What can you do to the “interaction”?

Robot Modelling

## - Jog each joint separately - Move the end-effector in cartesian space - Actuate torque at the joint’s level - Give a motion trajectory for the robot to follow - Given an external force to the chassis of a robot

# Giving & Getting Physical Quantities

Robot Modelling

Robot Modelling

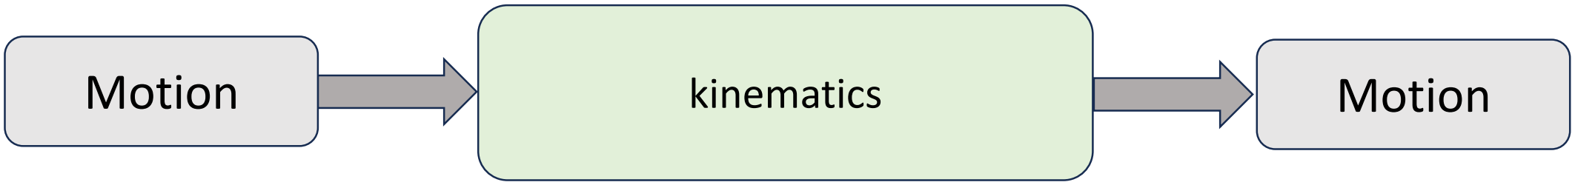
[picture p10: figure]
Motion; kinematics

Robot Modelling

Kinematics: study of motion regardless of force

Robot Modelling

in joint space | in taskspace

Robot Modelling

in joint space | in taskspace

Robot Modelling

in joint space | in taskspace

Robot Modelling

in taskspace | in joint space

Robot Modelling

Robot Modelling

Robot Modelling

Robot Modelling

Robot Modelling

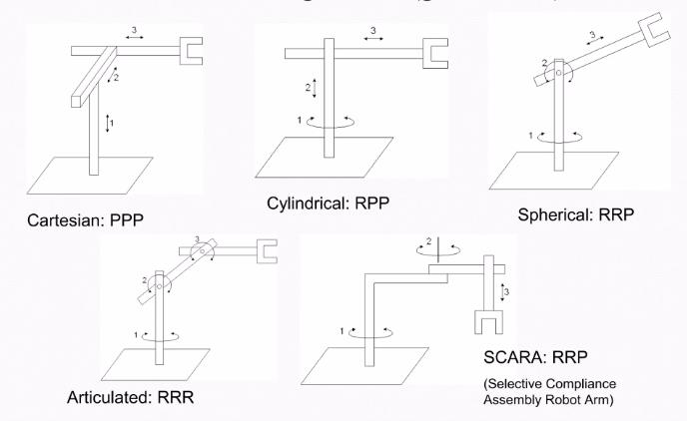
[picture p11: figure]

## Kinematics Model

## Dynamics Model

# Robot Model: Kinematics & Dynamics

# Rigid Body &Coordinate Frame

## - To describe the physical properties of

## a rigid body, one needs at least one reference “coordinate frame” - This frame is known as the “body-

attached” frame or “body” frame.

## Q.) Does a coordinate frame need to have a body?

Robot Modelling

# Tracking a pose

We can track a pose of an entire body by only tracking a pose of its body frame.

Robot Modelling

# Coordinate Frame

## Coordinate Frame consists of - an origin that describes its position - 3 orthogonal axes that describes its orientation

Fℬ

Robot Modelling

# Global Simulation Frame

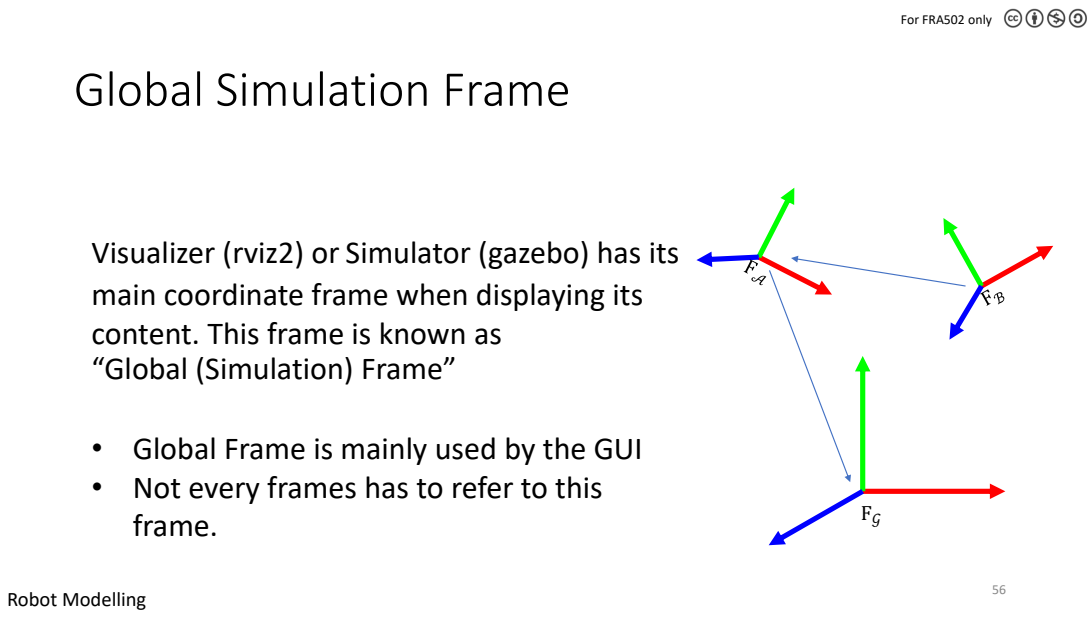
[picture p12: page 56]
frame.; Robot Modelling

Visualizer (rviz2) or Simulator (gazebo) has its
main coordinate frame when displaying its
content. This frame is known as
“Global (Simulation) Frame”

• Global Frame is mainly used by the GUI
• Not every frames has to refer to this

# Transform

# Transform

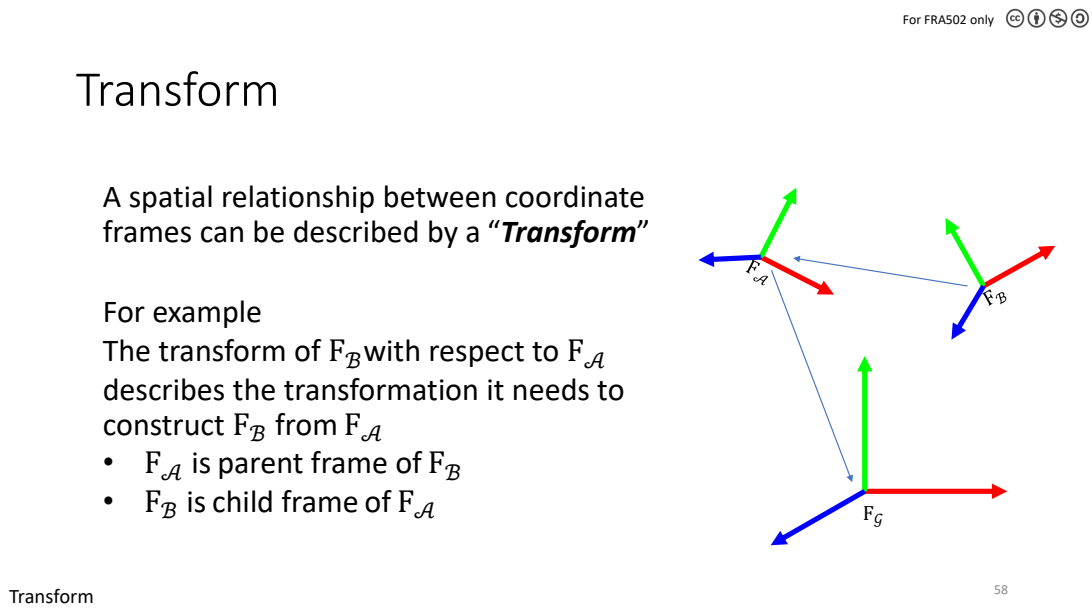
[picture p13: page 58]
Transform

A spatial relationship between coordinate
frames can be described by a “Transform”

For example
The transform of Fℬwith respect to FA
describes the transformation it needs to
construct Fℬ from FA
• FA is parent frame of Fℬ
• Fℬ is child frame of FA

# Components of a Transform

## Rotation :3 DOF - Quaternion: q = qx, qy, qz

, qw

## Translation : 3 DOF - Vector3 : p = px, py, pz

Transform

# Keeping track of Transforms

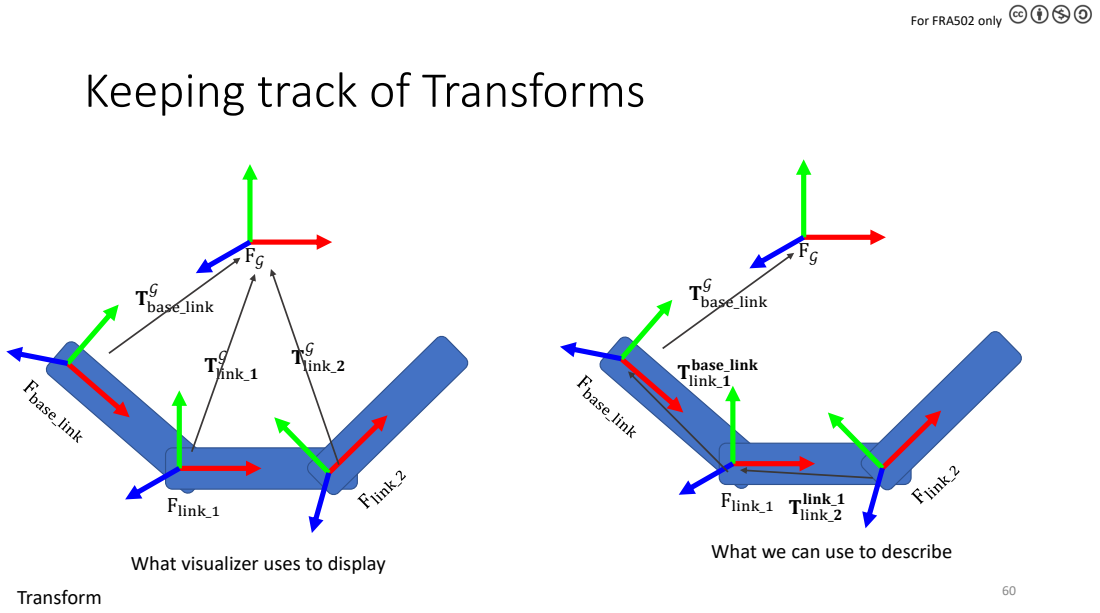
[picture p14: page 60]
60 Transform; Flink_1; Tbase_link; Tlink_1; Tlink_2; base_link; link_1

What we can use to describe What visualizer uses to display

tf2

We don’t have to create a system that track all coordinate frames. ROS2 already has a very special topic for this feature, which is known as tf2 .

ROS2 uses a topic “/tf”, which is an array of TransformStamped , to keep track of an entire tree (or multiple trees) in the system.

Transform

# tf2 in reality: tf & tf_static

To optimize the performance, the system usually has 2 Transform trees:
- /tf : this regular tf is used to describe “varying” transforms such as a pose of a mobile robot w.r.t. a fixed landmark.
- /tf_static: this tf is used to describe any fixed transforms such as the pose between lidar link and its attached chassis.

Transform

# tf2 in reality: tf & tf_static

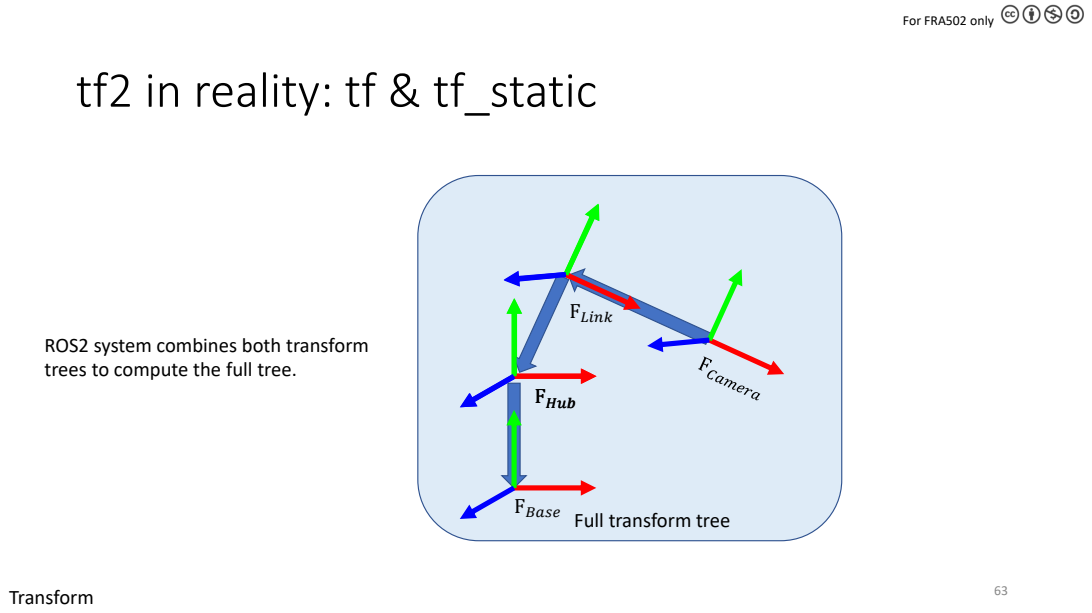
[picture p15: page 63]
Transform; FHub; FLink

ROS2 system combines both transform
trees to compute the full tree.

FBase
Full transform tree

# tf2 in reality: tf & tf_static

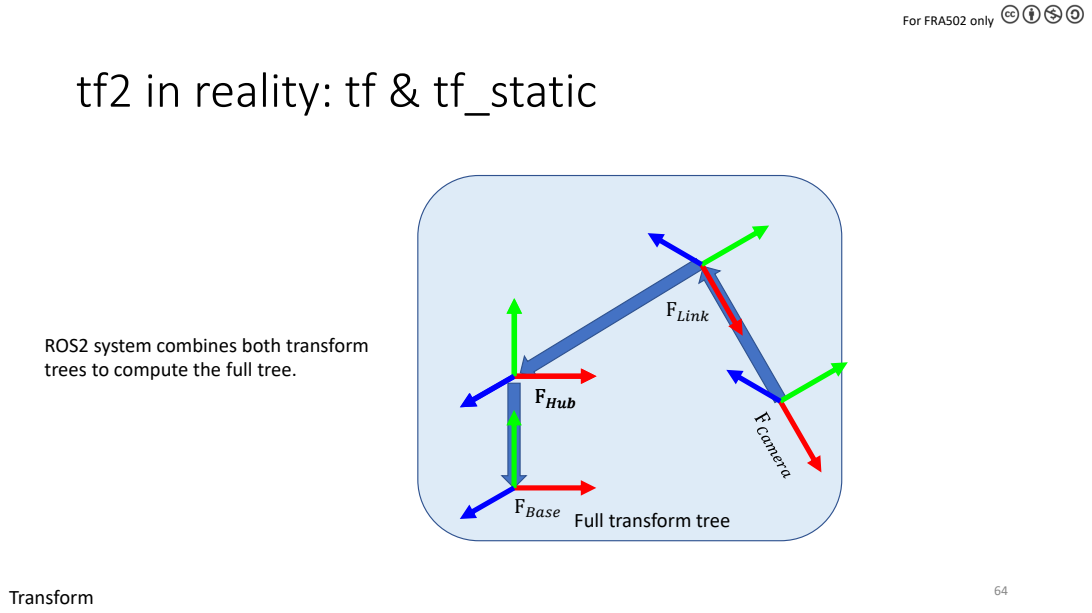
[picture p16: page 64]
Transform; FHub; FLink

ROS2 system combines both transform
trees to compute the full tree.

FBase
Full transform tree

# Transform

Transform

# TransformBroadcaster

**Broadcasting means partially update a topic.

Transform

# Example: TF2 from Turtlesim

## World Frame (W) : /world Robot Frame (R) : /{turtlename}

Transform

# Visualization

# Visualizer vs (Physics) Simulator

## - For visualizing only - Display whatever we tell them to

## - Has physics engine - Calculate motion and dynamics of the entire system, then display them

Visualization

# rviz2

/tf

We can use rviz to
visualize frames
from /tf, but we
need more than that
to display an entire
robot.

Visualization

# robot_description

/tf

“robot_description” is a default topic that /robot_description describes an appearance of a robot.

- “robot_description” is “std_msgs/String”
- The string must be written in a “specific” xml format .
- We can write a node to create the string, and publish to rviz, but someone already did that.

Visualization

Show the robot

Show the coordinate frames

# robot_description

Visualization

# robot_description

Visualization

# robot_state_publisher

A node called “robot_state_publisher” will take a URDF file and joint states to compute forward kinematics and generate messages to both “robot_description” and “tf” automatically. !!

Visualization

# What we must do for displaying a robot in rviz2

75 Visualization

# The structure of {robot’s name}_description

[pkg]

Visualization

# URDF: Unified Robotics Description Format

# URDF

# A format for describing the appearance and physical

parameters of any open-kinematics chain.

URDF: Unified Robotics Description Format

Links | Joints

# Link

# visual

# inertial

# collision

## link’s appearance: predefined shape, or mesh file Inertial parameters: for physics engine to compute its dynamics Collision Profile: for physics engine to compute collision dynamics

URDF: Unified Robotics Description Format

# Link

1 (http://wiki.ros.org/urdf/XML/link#CA-3f2893626f14a784b3d26cf27078c62b79d36f23_1) | <link name="my_link">
2 (http://wiki.ros.org/urdf/XML/link#CA-3f2893626f14a784b3d26cf27078c62b79d36f23_2) | <inertial>
3 (http://wiki.ros.org/urdf/XML/link#CA-3f2893626f14a784b3d26cf27078c62b79d36f23_3) | <origin xyz="0 0 0.5" rpy="0 0 0"/>
4 (http://wiki.ros.org/urdf/XML/link#CA-3f2893626f14a784b3d26cf27078c62b79d36f23_4) | <mass value="1"/>
5 (http://wiki.ros.org/urdf/XML/link#CA-3f2893626f14a784b3d26cf27078c62b79d36f23_5) | <inertia ixx="100" | ixy="0" | ixz="0" iyy="100" iyz="0" izz="100" />
6 (http://wiki.ros.org/urdf/XML/link#CA-3f2893626f14a784b3d26cf27078c62b79d36f23_6) | </inertial>
7 (http://wiki.ros.org/urdf/XML/link#CA-3f2893626f14a784b3d26cf27078c62b79d36f23_7)
8 (http://wiki.ros.org/urdf/XML/link#CA-3f2893626f14a784b3d26cf27078c62b79d36f23_8) | <visual>
9 (http://wiki.ros.org/urdf/XML/link#CA-3f2893626f14a784b3d26cf27078c62b79d36f23_9) | <origin xyz="0 0 0" rpy="0 0 0" />
10 (http://wiki.ros.org/urdf/XML/link#CA-3f2893626f14a784b3d26cf27078c62b79d36f23_10) | <geometry>
11 (http://wiki.ros.org/urdf/XML/link#CA-3f2893626f14a784b3d26cf27078c62b79d36f23_11) | <mesh file=file://$(find description_pkg)/meshes/>
12 (http://wiki.ros.org/urdf/XML/link#CA-3f2893626f14a784b3d26cf27078c62b79d36f23_12) | </geometry>
13 (http://wiki.ros.org/urdf/XML/link#CA-3f2893626f14a784b3d26cf27078c62b79d36f23_13) | <material name="Cyan">
14 (http://wiki.ros.org/urdf/XML/link#CA-3f2893626f14a784b3d26cf27078c62b79d36f23_14) | <color rgba="0 1.0 1.0 1.0"/>
15 (http://wiki.ros.org/urdf/XML/link#CA-3f2893626f14a784b3d26cf27078c62b79d36f23_15) | </material>
16 (http://wiki.ros.org/urdf/XML/link#CA-3f2893626f14a784b3d26cf27078c62b79d36f23_16) | </visual>
17 (http://wiki.ros.org/urdf/XML/link#CA-3f2893626f14a784b3d26cf27078c62b79d36f23_17)
18 (http://wiki.ros.org/urdf/XML/link#CA-3f2893626f14a784b3d26cf27078c62b79d36f23_18) | <collision>
19 (http://wiki.ros.org/urdf/XML/link#CA-3f2893626f14a784b3d26cf27078c62b79d36f23_19) | <origin xyz="0 0 0" rpy="0 0 0"/>
20 (http://wiki.ros.org/urdf/XML/link#CA-3f2893626f14a784b3d26cf27078c62b79d36f23_20) | <geometry>
21 (http://wiki.ros.org/urdf/XML/link#CA-3f2893626f14a784b3d26cf27078c62b79d36f23_21) | <cylinder radius="1" length="0.5"/>
22 (http://wiki.ros.org/urdf/XML/link#CA-3f2893626f14a784b3d26cf27078c62b79d36f23_22) | </geometry>
23 (http://wiki.ros.org/urdf/XML/link#CA-3f2893626f14a784b3d26cf27078c62b79d36f23_23) | </collision

URDF: Unified Robotics Description Format

# Link (example)

1 (http://wiki.ros.org/urdf/XML/link#CA-3f2893626f14a784b3d26cf27078c62b79d36f23_1) | <link name="my_link">
2 (http://wiki.ros.org/urdf/XML/link#CA-3f2893626f14a784b3d26cf27078c62b79d36f23_2) | <inertial>
3 (http://wiki.ros.org/urdf/XML/link#CA-3f2893626f14a784b3d26cf27078c62b79d36f23_3) | <origin xyz="0 0 0.5" rpy="0 0 0"/>
4 (http://wiki.ros.org/urdf/XML/link#CA-3f2893626f14a784b3d26cf27078c62b79d36f23_4) | <mass value="1"/>
5 (http://wiki.ros.org/urdf/XML/link#CA-3f2893626f14a784b3d26cf27078c62b79d36f23_5) | <inertia ixx="100" | ixy="0" | ixz="0" iyy="100" iyz="0" izz="100" />
6 (http://wiki.ros.org/urdf/XML/link#CA-3f2893626f14a784b3d26cf27078c62b79d36f23_6) | </inertial>
7 (http://wiki.ros.org/urdf/XML/link#CA-3f2893626f14a784b3d26cf27078c62b79d36f23_7)
8 (http://wiki.ros.org/urdf/XML/link#CA-3f2893626f14a784b3d26cf27078c62b79d36f23_8) | <visual>
9 (http://wiki.ros.org/urdf/XML/link#CA-3f2893626f14a784b3d26cf27078c62b79d36f23_9) | <origin xyz="0 0 0" rpy="0 0 0" />

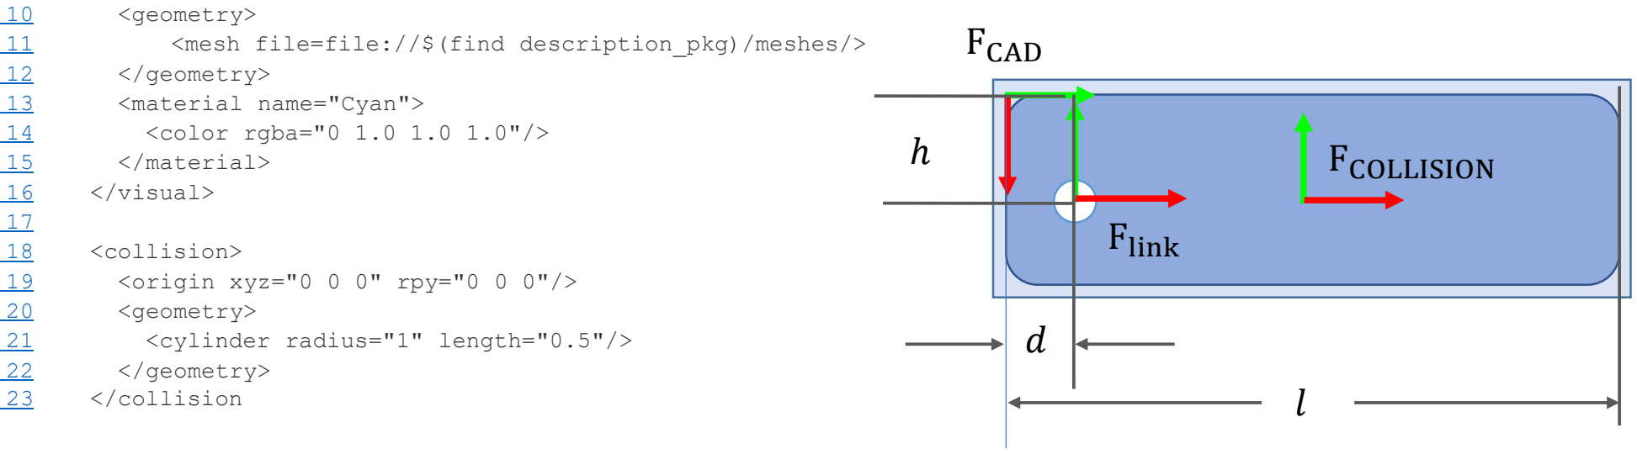
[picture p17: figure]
<geometry>; <mesh file=file://$(find description_pkg)/meshes/>; </geometry>; <material name="Cyan">; <color rgba="0 1.0 1.0 1.0"/>; </material>; </visual>; <collision>; <origin xyz="0 0 0" rpy="0 0 0"/>; <cylinder radius="1" length="0.5"/>; </collision; Flink; FCAD; FCOLLISION

URDF: Unified Robotics Description Format

# Joint

## Types: - Revolute - Continuous - Prismatic - Fixed - Floating - planar

URDF: Unified Robotics Description Format

# Joint

1 (http://wiki.ros.org/urdf/XML/joint#CA-7f33094f9f37ce5633c81521283ac23bf757efba_1) | <joint name="my_joint" type="floating">
2 (http://wiki.ros.org/urdf/XML/joint#CA-7f33094f9f37ce5633c81521283ac23bf757efba_2) | <origin xyz="0 0 1" rpy="0 0 3.1416"/>
3 (http://wiki.ros.org/urdf/XML/joint#CA-7f33094f9f37ce5633c81521283ac23bf757efba_3) | <parent link="link1"/>
4 (http://wiki.ros.org/urdf/XML/joint#CA-7f33094f9f37ce5633c81521283ac23bf757efba_4) | <child link="link2"/>
5 (http://wiki.ros.org/urdf/XML/joint#CA-7f33094f9f37ce5633c81521283ac23bf757efba_5)
6 | <dynamics damping="0.0" friction="0.0"/>
7 | <limit effort="30" velocity="1.0" lower="-2.2" upper="0.7" />
8
9 </joint>

URDF: Unified Robotics Description Format

Fixed transformation before the actuation

# URDF File’s content

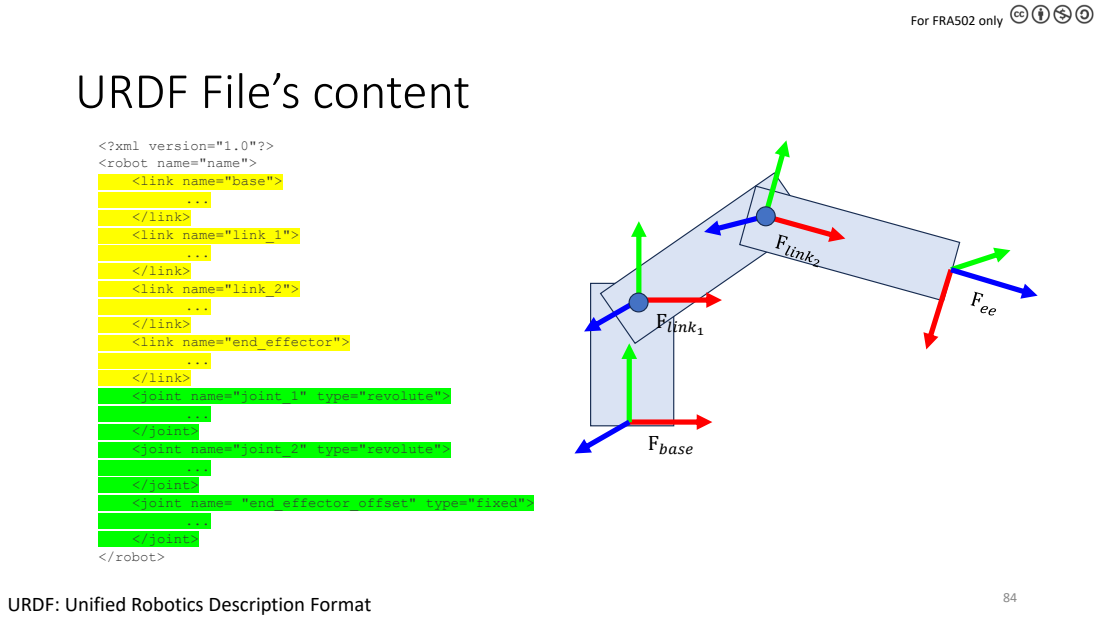
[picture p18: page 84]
</joint>; </robot>; Flink1; Fbase

<?xml version="1.0"?>
<robot name="name">

<link name="base">

</link>
<link name="link_1">

<link name="link_2">

<link name="end_effector">

<joint name="joint_1" | | type="revolute">

<joint name="joint_2" type="revolute">

</joint>
<joint name= "end_effector_offset" type="fixed">

URDF: Unified Robotics Description Format

# Where do we put our URDF

Visualization

# From URDF to RVIZ

URDF | RVIZ

URDF: Unified Robotics Description Format

# From URDF to RVIZ

URDF does not describe what the robot is currently doing, but RVIZ requires its current state.

URDF: Unified Robotics Description Format

# joint_state_publisher

URDF: Unified Robotics Description Format

# General steps for displaying a robot URDF in RVIZ

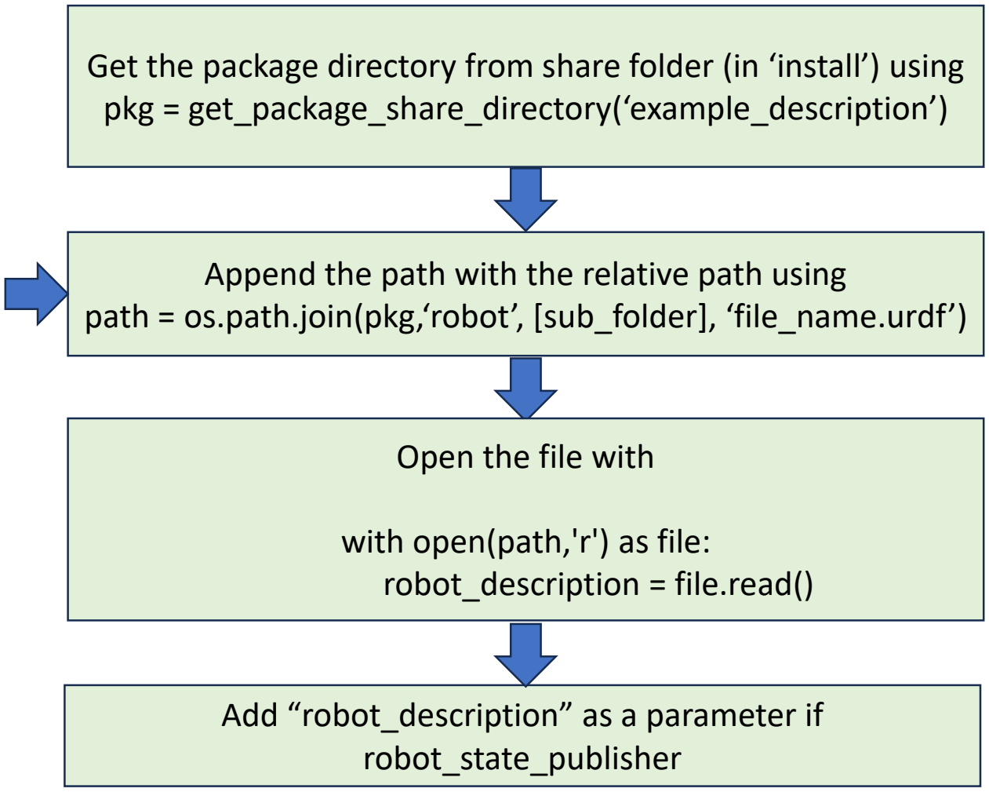
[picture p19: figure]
pkg = get_package_share_directory(‘example_description’); path = os.path.join(pkg,‘robot’, [sub_folder], ‘file_name.urdf’); Open the file with; with open(path,'r') as file: robot_description = file.read(); robot_state_publisher

Get the package directory from share folder (in ‘install’) using

Append the path with the relative path using ‘file_name.urdf’

Add “robot_description” as a parameter if

# Example

robot

Package:
my_robot_description

URDF: Unified Robotics Description Format

visual

my_robot.urdf

# Example

robot

Package:
my_robot_description

URDF: Unified Robotics Description Format

visual

my_robot.urdf

from launch import LaunchDescription

def generate_launch_description()

launch_description = LaunchDescription()

return launch_description

# Example

robot

Package:
my_robot_description

URDF: Unified Robotics Description Format

visual

my_robot.urdf

from launch import LaunchDescription from launch_ros.actions import Node

def generate_launch_description()

path = ...

robot_state_publisher = Node(
package = 'robot_state_publisher',
executable = 'robot_state_publisher', parameters = [{'robot_description':robot_desc}] )

launch_description = LaunchDescription()

launch_description.add_action(robot_state_publisher)

return launch_description

# Example

robot

Package:
my_robot_description

URDF: Unified Robotics Description Format

visual

my_robot.urdf

from launch import LaunchDescription from launch_ros.actions import Node

def generate_launch_description()

pkg = get_package_share_directory('my_robot_description')

path = os.path.join(pkg,'robot','visual','my_robot.urdf')

with open(path,'r’) as file:
robot_desc = file.read()

robot_state_publisher = Node(
package = 'robot_state_publisher',
executable = 'robot_state_publisher', parameters = [{'robot_description':robot_desc}] )

launch_description = LaunchDescription()

launch_description.add_action(robot_state_publisher)

return launch_description

# Example

robot

Package:
my_robot_description

URDF: Unified Robotics Description Format

visual

my_robot.urdf

from launch import LaunchDescription from launch_ros.actions import Node

def generate_launch_description()

robot_state_publisher = ...

rviz = ...

joint_state_publisher_gui = ...

launch_description = LaunchDescription()

launch_description.add_action(robot_state_publisher)

launch_description.add_action(rviz)

launch_description.add_action(joint_state_publisher_gui)

return launch_description

# Robot Parameters

# Parameters vs. Models

Robot Parameters

- A robot model is a mathematical representation of a robot.
- A robot parameter is a numerical value that is used to describe robot’s property.

# Example: Serial Manipulator

Robot Parameters

# Possible Software Implementation

Parameters will be assigned in a YAML file.

As of now, one can only hard-code the

# Example: Differential Drive Robot

99 Robot Parameters

# [name]_description

parameters.yaml

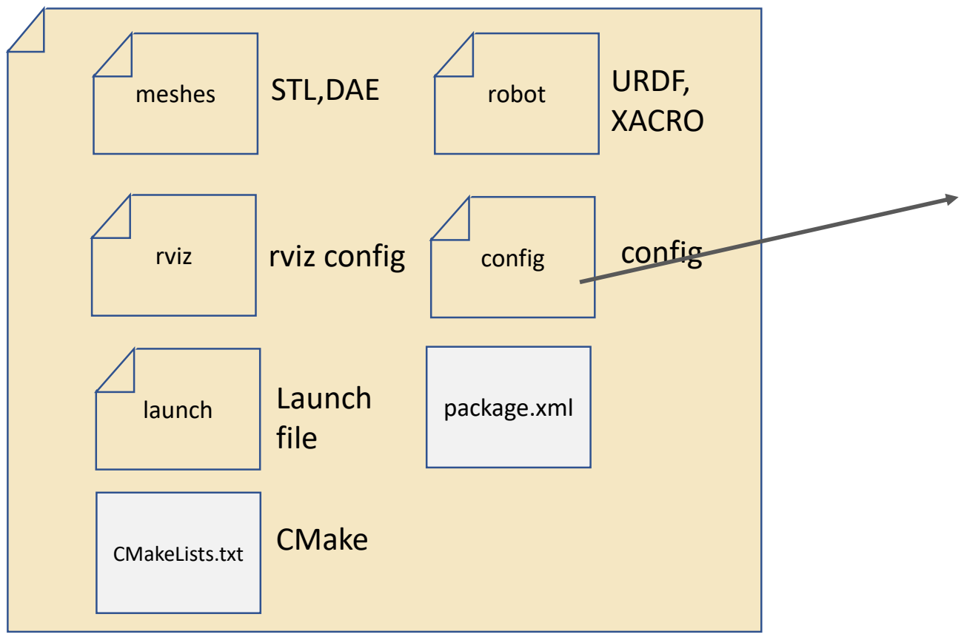
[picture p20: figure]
meshes; robot; rviz; CMakeLists.txt; launch; package.xml; STL,DAE; URDF,; XACRO; config; Launch file; CMake; rviz config

Robot Parameters

# example_description

kinematics_parameter.yaml

Robot Parameters

base:
orientation: 0.0 0.0 0.0
position: 0.0 0.0 0.0
types:
- revolute
- revolute
- revolute
links:
- orientation: 0.0 0.0 0.0
position: 0.0 0.0 0.2
- orientation: 0.0 -1.5707963267948966 -1.5707963267948966 position: 0.0 -0.12 0.0
- orientation: 0.0 0.0 0.0
position: 0.25 0.0 0.1
joints:
- lower: -3.141592653589793 upper: 3.141592653589793
velocity: 1000.0
effort: 1000.0
- lower: -3.141592653589793 upper: 3.141592653589793
velocity: 1000.0
effort: 1000.0
- lower: -3.141592653589793 upper: 3.141592653589793
velocity: 1000.0
effort: 1000.0
end_effector:
orientation: 1.5707963267948966 0.0 1.5707963267948966 position: 0.28 0.0 0.0

# Limitation of URDF

# We cannot use common

parameters.

# We have to write every single

part regardless of their copies.

Robot Parameters

# What if ?

# 1 long

URDF file.

Robot Parameters

# xacro : XML macros

# What can we do with xacro?

We can use xacro to define macros in xml format.

URDF is also an xml.

xacro : XML macros

# Processing xacro file in command line

Before generating a file, it is time-saving to test whether the resultant URDF file can be correctly generated. One can use the following command to test their xacro file.

>>xacro [xacro_file.xacro] [optional arguments] > [urdf_file.urdf]

Open the generated URDF file to check the content. If errors exist in the xacro file, “xacro” process will display the corresponding error message.

xacro : XML macros

# Processing xacro file in Python Launch script

To obtain “robot_description” from the xacro file, one can use the following function.

robot_description = xacro.process_file(full_path_to_xacro_file).toxml()

This is equivalent to reading a URDF file.

xacro : XML macros

# Performing basic arithmetics

# xacro recognizes a tag “${}” as performing calculation. Therefore, you do not have to compute

the parameters manually.

### <origin xyz=“${1/2} ${2+3} ${2*4}” />

### <origin xyz=“0.5 5 8” />

xacro : XML macros

# Defining a macro

“macro” is a substitution. One can also pass parameters to a macro.

<xacro:macro name=“something” params=“param1 param2 param3”>

<visual>
<geometry>
<box size=“${param1} ${param2} ${param3}”> </geometry>
</visual>
</xacro:macro>

Anything can be put inside the macro.

xacro : XML macros

# Using the macro

<xacro:something param1=“0.2” param2=“0.3” param3=“0.4”/>

<visual>
<geometry>
<box size=“0.2 0.3 0.4”>
</geometry>
</visual>

xacro : XML macros

# Using the macro

<robot>
<link name=“base”/>
<xacro:robot_link index=“0”/> <xacro:robot_link index=“1”/> <xacro:robot_link index=“2”/> <xacro:robot_link index=“3”/> <link name=“end_effector”/> <xacro:base_offset/>
<xacro:robot_joint index=“1”/> <xacro:robot_joint index=“2”/> <xacro:robot_joint index=“3”/> <xacro:end_effector_offset/> </robot>

xacro : XML macros

# Including another file

When you include another xacro file, you essential put all its content in the file.

<xacro:include filename=“$(find package_name)/sub_folder/other_file.xacro”/>

Anything from the included file will be put in this file.

xacro : XML macros

# Declaring a property

A “property” in xacro is global. Once it is declared, any subsequent lines can access its value.

<xacro:property name=“foo” value=“1.5”/>

xacro : XML macros

# Using the property

# One can use the calculation tag to substitute the value of the property

### <origin xyz=“${foo} ${foo/2} ${foo*1.5}” />

xacro : XML macros

# Open dictionary from YAML

<xacro:property name="params_path" value="$(find name_description)/config/parameters.yaml"/>

<xacro:property name="my_dict" value="${xacro.load_yaml(params_path)}"/>

<xacro:property name=“param_1" value="${my_dict[‘key_1’]}"/>

<xacro:property name=“param_2" value="${my_dict[‘key_2’][‘key_a’]}"/>

xacro : XML macros

“find” acts like “get_package_share_directory”

# Using “if”

# “if” allows one to conditionally create an xacro expression. If the value is evaluated as True, the

expression inside will be generated.

<xacro:if value=“${name==‘left’}”> <xacro:property name=“y” value=“${d}”> </xacro:if>

xacro : XML macros

# Using “unless”

# “unless” also allows one to negate the condition. If the value is evaluated as False, the expression inside

will be generated.

<xacro:unless value=“${name==‘left’}”> <xacro:property name=“y” value=“${-d}”> </xacro:unless>

xacro : XML macros

# Possible xacro file management

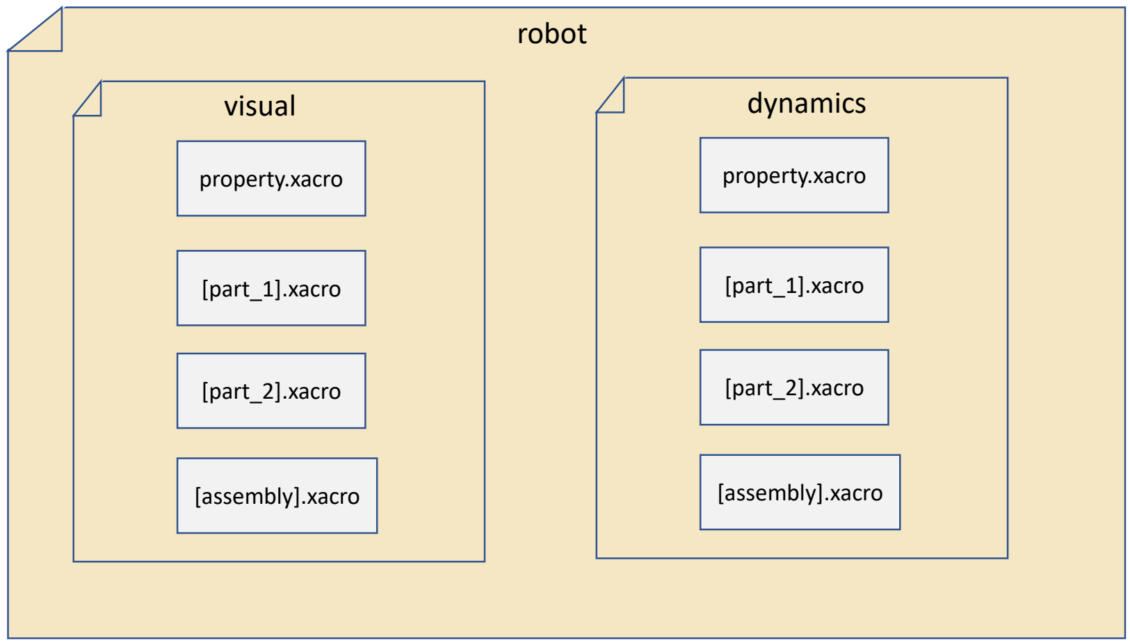
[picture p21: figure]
property.xacro; visual; robot; [part_1].xacro; [part_2].xacro; [assembly].xacro; dynamics

xacro : XML macros

# property.xacro

xacro : XML macros

<?xml version='1.0'?>
<robot xmlns:xacro="http://www.ros.org/wiki/xacro">

<xacro:property name="description_package" value="example_description"/>

<!-- File paths-->
<xacro:property name="params_path" value="$(find ${description_package})/config/parameters.yaml"/> <xacro:property name="param_dict" value="${xacro.load_yaml(params_path)}"/>

<!-- Mathematics Constants -->
<xacro:property name="PI" value="3.1415926535897931"/>

<!-- Robot Properties -->
<xacro:property name="LENGTH" value="${param_dict['length']}"/> <xacro:property name="WIDTH" value="${param_dict['width']}"/> <xacro:property name="OFFSET" value="${param_dict['offset']}"/>

</robot>

# [part_1].xacro

xacro : XML macros

<?xml version='1.0'?>
<robot xmlns:xacro="http://www.ros.org/wiki/xacro">

<xacro:macro name= "my_macro" params="id"> <visual>
<origin xyz="${OFFSET[id-1]}"/>
<geometry>
<mesh filename="file://$(find example_description)/meshes/link_${id-1}.stl"/> </geometry>
<material name="link_color">
<color rgba="${COLOR[id-1]}"/>
</material>
</visual>
</xacro:macro>

</robot>

# [assembly].xacro

xacro : XML macros

<?xml version='1.0'?>
<robot xmlns:xacro="http://www.ros.org/wiki/xacro" name="example" > <xacro:arg name="robot_name" default=""/>
<xacro:property name="namespace" value="$(arg robot_name)"/>

<xacro:include filename="$(find example_description)/robot/visual/properties.xacro"/> <xacro:include filename="$(find example_description)/robot/visual/part_1.xacro"/>

<link name=base>
<xacro:my_macro id="0"/>
</link>

<link name=link_1>
<xacro:my_macro id="1"/>
</link>

<joint name="joint_1">
</joint>

</robot>

# Processing xacro file in command line

Before generating a file, it is time-saving to test whether the resultant URDF file can be correctly generated. One can use the following command to test their xacro file.

>>xacro [xacro_file.xacro] [optional arguments] > [urdf_file.urdf]

Open the generated URDF file to check the content. If errors exist in the xacro file, “xacro” process will display the corresponding error message.

xacro : XML macros

# Processing xacro file in Python Launch script

To obtain “robot_description” from the xacro file, one can use the following function.

robot_description = xacro.process_file(full_path_to_xacro_file).toxml()

This is equivalent to reading a URDF file.

xacro : XML macros

# What do we have so far ?

# - A way to display a robot in rviz

xacro : XML macros

# What do we have so far ?

# - A way to display a robot in rviz

xacro : XML macros

## What if we want to display 2 identical robots simultaneously?

# Concern 1: File Duplication

# One can create a file that auto-generates a new set of robot description xacro files with the added

namespace.

# This works okay if we have several robots. But we can

be more efficient.

xacro : XML macros

# Concern 2: Connecting tree

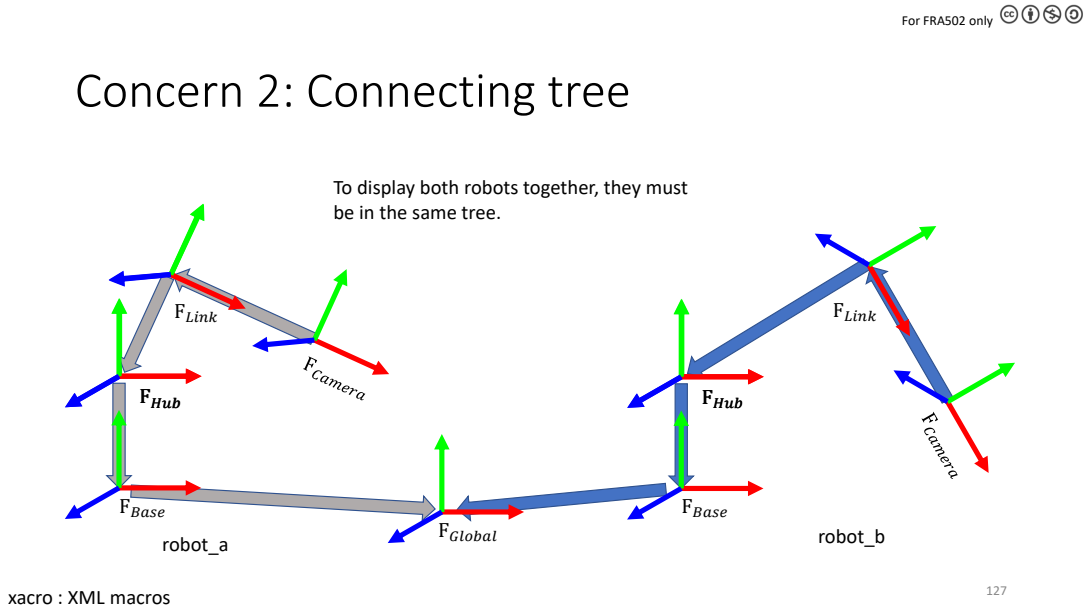
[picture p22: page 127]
FHub; robot_b; FBase; FLink; robot_a; FGlobal

To display both robots together, they must
be in the same tree.

xacro : XML macros

# Concern 2: Connecting tree

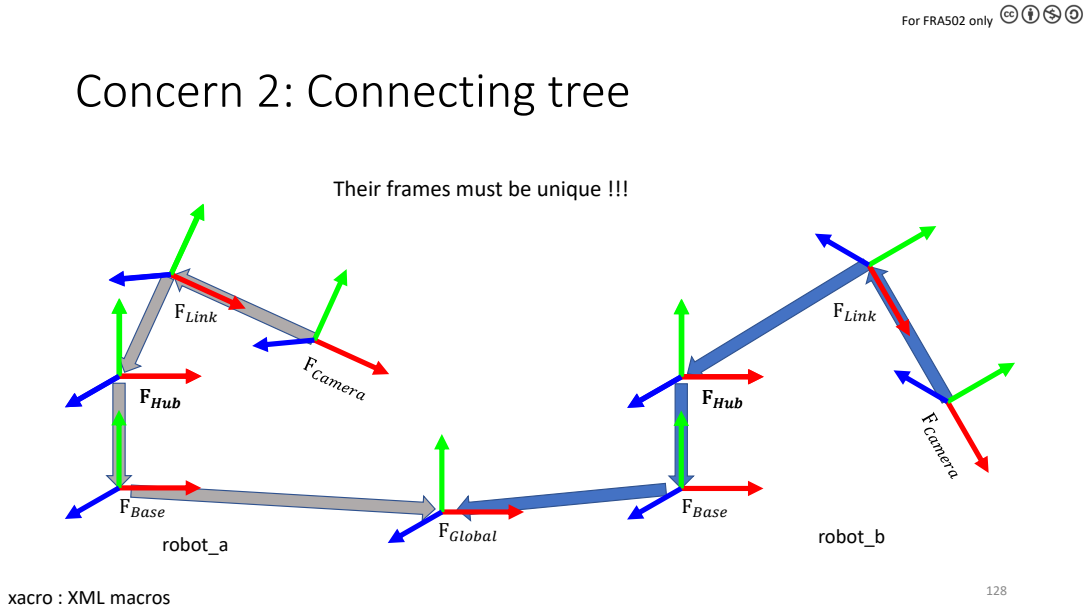
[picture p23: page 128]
FHub; robot_b; FBase; FLink; robot_a; FGlobal

Their frames must be unique !!!

xacro : XML macros

# Frame Prefix

# Resolving conflict using Frame Prefix

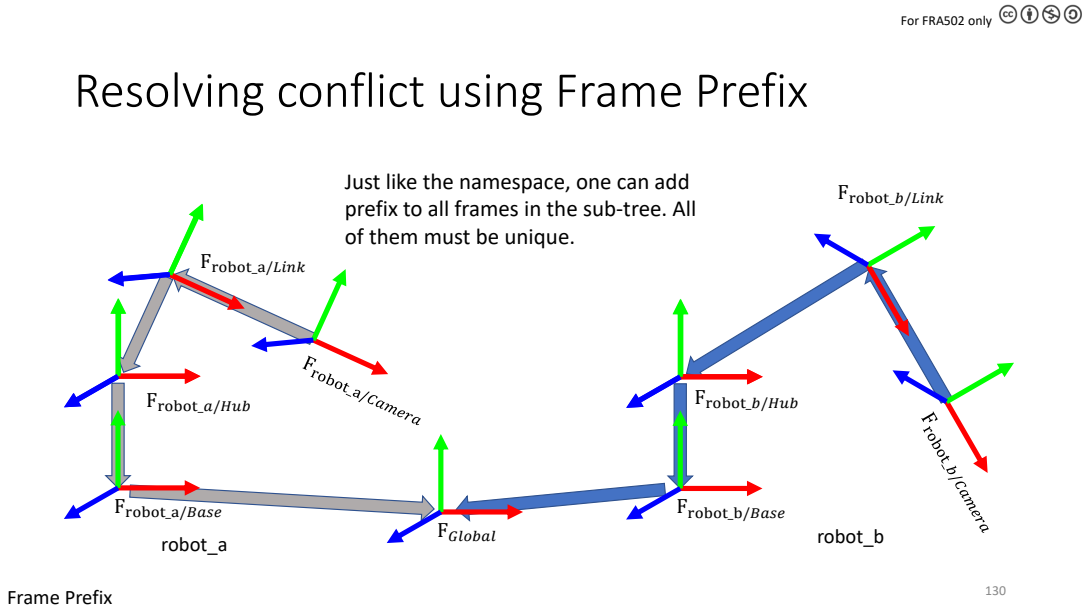
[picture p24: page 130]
130 Frame Prefix; Frobot_b/Hub; robot_b; Frobot_b/Base; Frobot_b/Link; Frobot_a/Link; robot_a; Frobot_a/Base; Frobot_a/Hub; FGlobal

Just like the namespace, one can add
prefix to all frames in the sub-tree. All
of them must be unique.
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

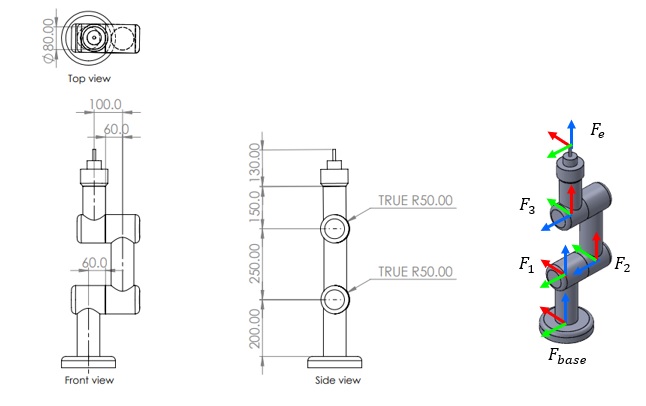
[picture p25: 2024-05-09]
f1tenth_ws/src/example_description/doc/robot_schematics.jpg

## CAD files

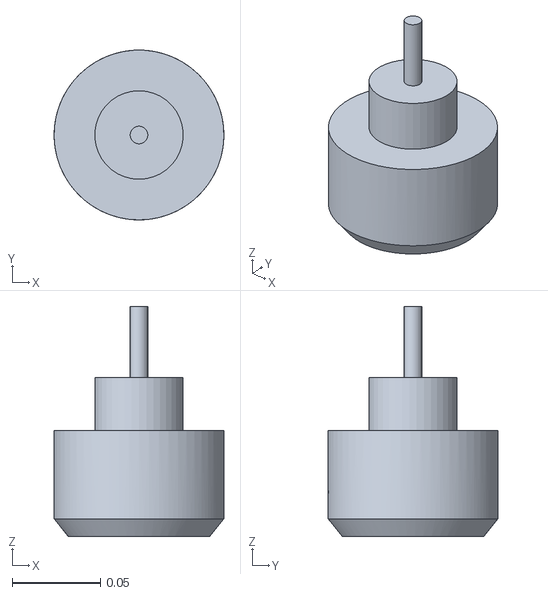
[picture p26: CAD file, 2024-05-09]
f1tenth_ws/install/example_description/share/example_description/meshes/end_effector.stl
0.096 x 0.096 x 0.13

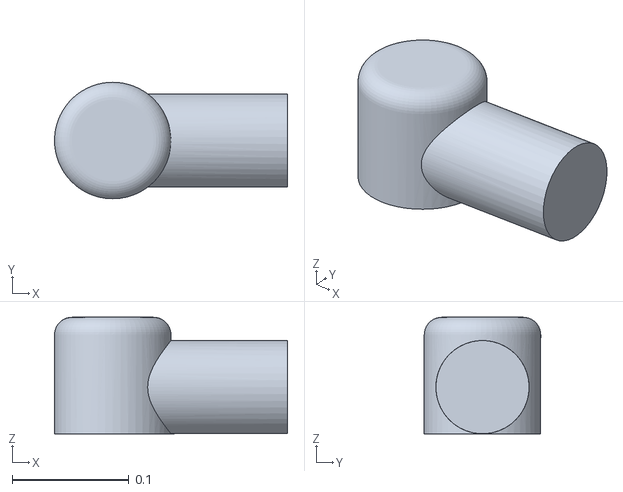
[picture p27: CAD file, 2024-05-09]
f1tenth_ws/install/example_description/share/example_description/meshes/link_3.stl
0.2 x 0.1 x 0.1

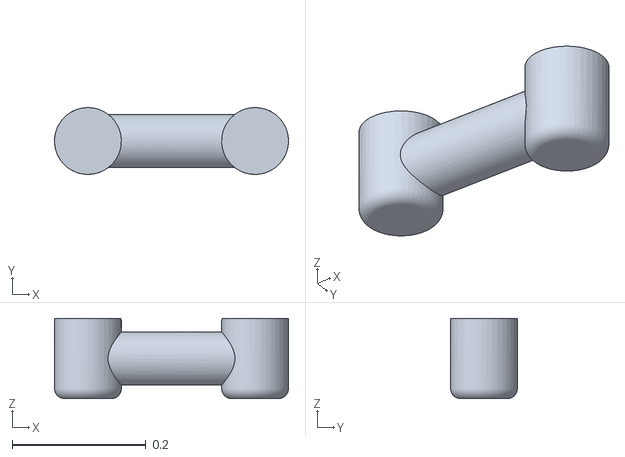
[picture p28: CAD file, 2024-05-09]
f1tenth_ws/install/example_description/share/example_description/meshes/link_2.stl
0.35 x 0.1 x 0.12

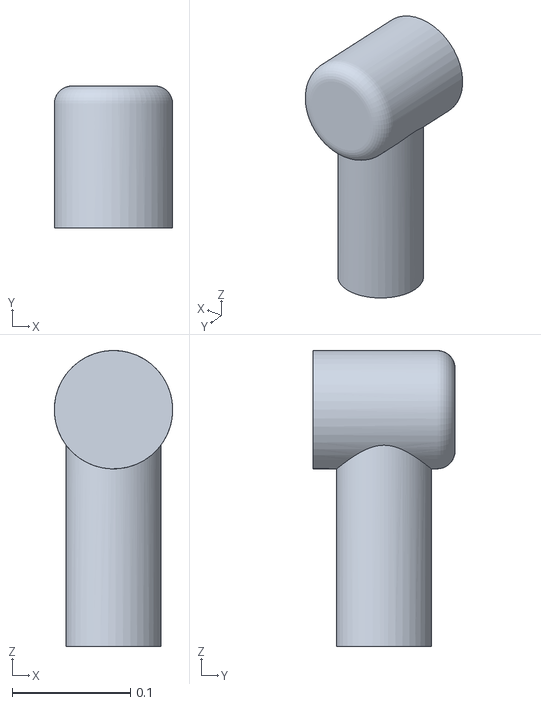
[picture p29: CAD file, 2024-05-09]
f1tenth_ws/install/example_description/share/example_description/meshes/link_1.stl
0.1 x 0.12 x 0.25

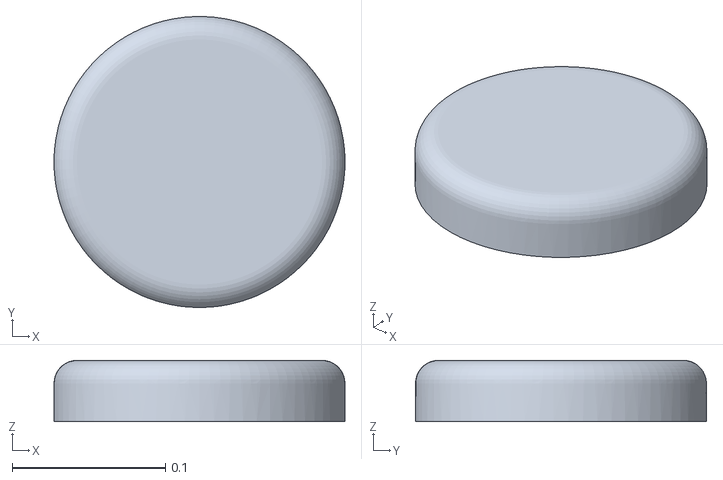
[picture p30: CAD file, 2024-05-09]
f1tenth_ws/install/example_description/share/example_description/meshes/link_base.stl
0.19 x 0.19 x 0.04

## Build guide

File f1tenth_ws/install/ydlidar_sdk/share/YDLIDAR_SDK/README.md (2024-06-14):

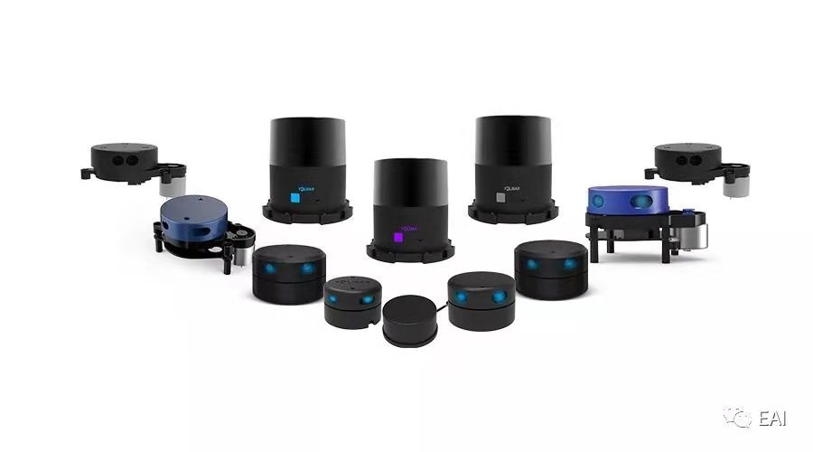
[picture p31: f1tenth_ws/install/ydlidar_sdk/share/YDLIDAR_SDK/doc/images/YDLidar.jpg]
YDLIDAR


# Table of Contents

1. [Table of Contents](#table-of-contents)
2. [Introduction](#introduction)
    - [Prerequisites](#prerequisites)
    - [Supported Languages](#supported-languages)
3. [YDLidar SDK Communication Protocol](#ydlidar-sdk-communication-protocol)
4. [Architecture](#architecture)
5. [Installation](#installation)
6. [Documents](#documents)
7. [Support](#support)
8. [Contact EAI](#contact-eai)

# Introduction

YDLidar SDK is the software development kit designed for all YDLIDAR products. It is developed based on C/C++ following YDLidar SDK Communication Protocol, and provides easy-to-use C/C++, Python, C# style API. With YDLidar SDK, users can quickly connect to YDLidar products and receive Laser scan data.

YDLidar SDK consists of YDLidar SDK communication protocol, YDLidar SDK core, YDLidar SDK API, Linux/windows samples, and Python demo.

### Prerequisites
* Linux
* Windows 7/10, Visual Studio 2015/2017(UTF-8 encoding)
* C++11 compiler

### Supported Languages
* C / C++
* Python
* C#

## YDLidar SDK Communication Protocol
YDLidar SDK communication protocol opens to all users. It is the communication protocol between user programs and YDLIDAR products. The protocol consists of control commands and data format. Please refer to the [YDLidar SDK Communication Protocol](doc/YDLidar-SDK-Communication-Protocol.md) for detailed information.

## Architecture

YDLidar SDK provides the implementation of control commands and Laser scan data transmission, as well as the C/C++,Python API. The basic structure of YDLidar SDK is shown as below:

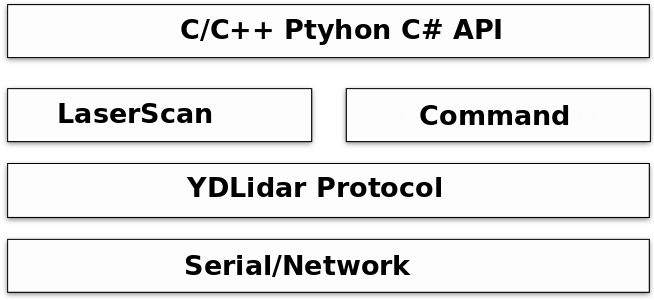
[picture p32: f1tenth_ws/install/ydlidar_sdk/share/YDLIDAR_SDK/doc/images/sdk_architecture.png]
YDLidar SDK Architecture


 Serial or network is used for communication between YDLidar SDK and LiDAR sensors. Please refer to the YDLidar SDK Communication Protocol for further information. LaserScan supports Laser Scan Data transmission, while Command handler receives and sends control commands. And the C++ API is based on Command and LaserScan Hander.

The YDLidar LiDAR sensors can be connected to host directly by serial or through the YDLidar Adapter board. YDLidar SDK supports both connection methods. When LiDAR units are connected to host directly by Serial, the host will establish communication with each LiDAR unit individually. And if the LiDAR units connect to host through Adapter board, then the host only communicates with the YDLidar Adapter board while the Adapter Board communicates with each LiDAR unit.

## Installation

* [Fork and then Clone YDLidar-SDK's GitHub code](https://github.com/YDLIDAR/YDLidar-SDK) 

* [Build and Install](doc/howto/how_to_build_and_install.md) - This step is required

## Documents
* [LiDAR Dataset](doc/Dataset.md): All you need to know about LiDAR Models.

* [SDK FlowChart](doc/Diagram.md): Development flowchart.

* [YDLIDAR SDK API for Developers](doc/YDLIDAR_SDK_API_for_Developers.md): All you need to know about YDLiDAR-SDK API

* [YDLIDAR SDK Communication Protocol](doc/YDLidar-SDK-Communication-Protocol.md): All you need to know about YDLiDAR-SDK Communication Protocol.

* [HowTo](doc/howto/README.md): Brief technical solutions to common problems that developers face during the installation and use of the YDLidar-SDk 

* [Tutorials](doc/Tutorials.md): Quick Tutorials

* [FAQs](doc/FAQs/README.md) 

## Support

You can get support from YDLidar with the following methods:
* Send email to support@ydlidar.com with a clear description of your problem and your setup
* Github Issues

## Contact EAI
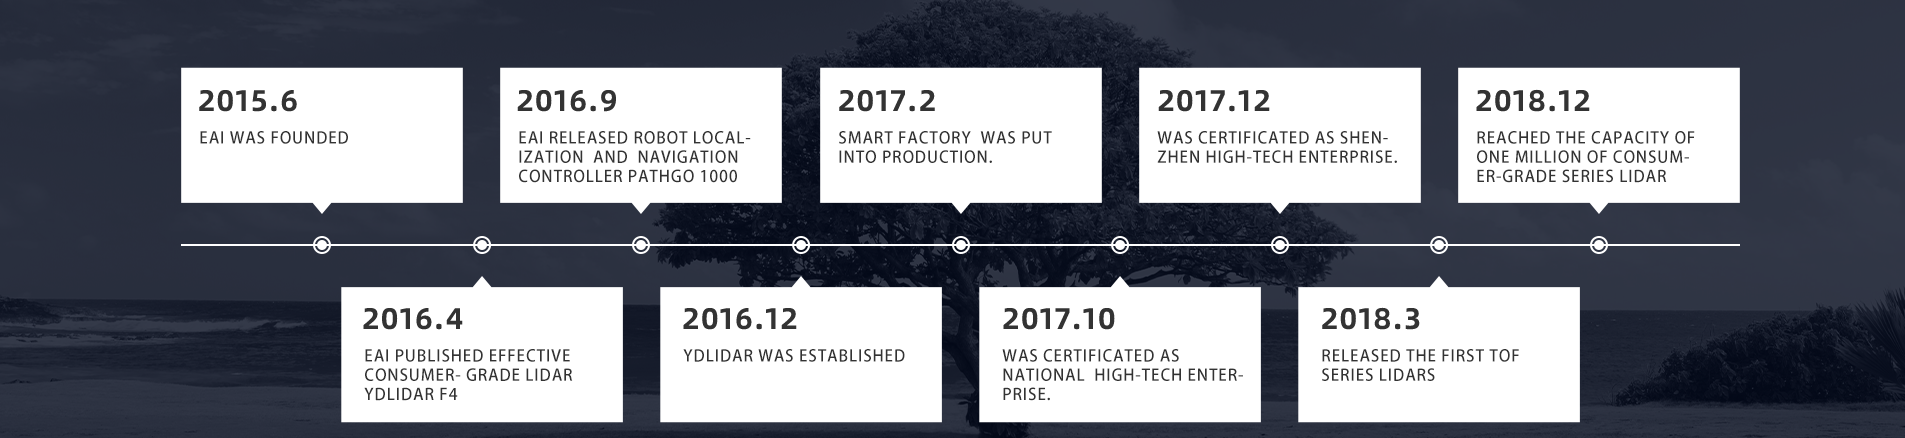
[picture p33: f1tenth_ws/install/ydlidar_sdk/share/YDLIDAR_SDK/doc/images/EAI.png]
Development Path


If you have any extra questions, please feel free to [contact us](http://www.ydlidar.cn/cn/contact)

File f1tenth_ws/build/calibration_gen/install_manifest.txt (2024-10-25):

/home/ubuntu/f1tenth_ws/install/calibration_gen/share/calibration_gen/environment/pythonpath.sh
/home/ubuntu/f1tenth_ws/install/calibration_gen/share/calibration_gen/environment/pythonpath.dsv
/home/ubuntu/f1tenth_ws/install/calibration_gen/local/lib/python3.10/dist-packages/calibration_gen-0.0.0-py3.10.egg-info/PKG-INFO
/home/ubuntu/f1tenth_ws/install/calibration_gen/local/lib/python3.10/dist-packages/calibration_gen-0.0.0-py3.10.egg-info/SOURCES.txt
/home/ubuntu/f1tenth_ws/install/calibration_gen/local/lib/python3.10/dist-packages/calibration_gen-0.0.0-py3.10.egg-info/top_level.txt
/home/ubuntu/f1tenth_ws/install/calibration_gen/local/lib/python3.10/dist-packages/calibration_gen-0.0.0-py3.10.egg-info/dependency_links.txt
/home/ubuntu/f1tenth_ws/install/calibration_gen/local/lib/python3.10/dist-packages/calibration_gen/euler_angle_estimation.py
/home/ubuntu/f1tenth_ws/install/calibration_gen/local/lib/python3.10/dist-packages/calibration_gen/__init__.py
/home/ubuntu/f1tenth_ws/install/calibration_gen/lib/calibration_gen/signal_generate.py
/home/ubuntu/f1tenth_ws/install/calibration_gen/lib/calibration_gen/imuread_node.py
/home/ubuntu/f1tenth_ws/install/calibration_gen/lib/calibration_gen/cal_node.py
/home/ubuntu/f1tenth_ws/install/calibration_gen/share/calibration_gen/config/sensor_calibration.yaml
/home/ubuntu/f1tenth_ws/install/calibration_gen/share/calibration_gen/config/config.yaml
/home/ubuntu/f1tenth_ws/install/calibration_gen/share/calibration_gen/config/sensor_calibration _dynamic.yaml
/home/ubuntu/f1tenth_ws/install/calibration_gen/share/calibration_gen/config/sensor_calibration_steady_state.yaml
/home/ubuntu/f1tenth_ws/install/calibration_gen/share/ament_index/resource_index/package_run_dependencies/calibration_gen
/home/ubuntu/f1tenth_ws/install/calibration_gen/share/ament_index/resource_index/parent_prefix_path/calibration_gen
/home/ubuntu/f1tenth_ws/install/calibration_gen/share/calibration_gen/environment/ament_prefix_path.sh
/home/ubuntu/f1tenth_ws/install/calibration_gen/share/calibration_gen/environment/ament_prefix_path.dsv
/home/ubuntu/f1tenth_ws/install/calibration_gen/share/calibration_gen/environment/path.sh
/home/ubuntu/f1tenth_ws/install/calibration_gen/share/calibration_gen/environment/path.dsv
/home/ubuntu/f1tenth_ws/install/calibration_gen/share/calibration_gen/local_setup.bash
/home/ubuntu/f1tenth_ws/install/calibration_gen/share/calibration_gen/local_setup.sh
/home/ubuntu/f1tenth_ws/install/calibration_gen/share/calibration_gen/local_setup.zsh
/home/ubuntu/f1tenth_ws/install/calibration_gen/share/calibration_gen/local_setup.dsv
/home/ubuntu/f1tenth_ws/install/calibration_gen/share/calibration_gen/package.dsv
/home/ubuntu/f1tenth_ws/install/calibration_gen/share/ament_index/resource_index/packages/calibration_gen
/home/ubuntu/f1tenth_ws/install/calibration_gen/share/calibration_gen/cmake/calibration_genConfig.cmake
/home/ubuntu/f1tenth_ws/install/calibration_gen/share/calibration_gen/cmake/calibration_genConfig-version.cmake
/home/ubuntu/f1tenth_ws/install/calibration_gen/share/calibration_gen/package.xml

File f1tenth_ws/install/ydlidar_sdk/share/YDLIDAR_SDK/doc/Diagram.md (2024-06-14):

# FlowChart

```flow
st=>start: Start
op=>operation: Set Paramamters and Initialize
op1=>operation: TrunOn
tr=>operation: Try Again
op2=>operation: doProcessSimple
op3=>operation: TrunOff
op4=>operation: disconnecting
cond=>condition: success Yes or No?
cond1=>condition: success Yes or No?
cond2=>condition: success Yes or No?
cond3=>condition: LOOP Yes or No?
cond4=>condition: TryAgain Yes or No?
e=>end: End
en=>end: End

st(left)->op->cond
cond(yes)->op1->cond1
cond(no)->op3->op4->e
cond1(yes)->op2->cond3
cond3(yes)->op2
cond3(no, left)->op3->op4->e
cond1(no,right)->tr(bottom)->cond4
cond4(yes)->op3
cond4(no)->op3(right)->op4(right)->e
```

# sequenceDiagram

```mermaid
sequenceDiagram
note over UserProgram: Set Paramters
note over UserProgram: Initialize SDK
UserProgram->Command: Get LiDAR Information
Command-->UserProgram: Device connected and Devce Information recevied
note over UserProgram: TurnOn
UserProgram->Command: Start LiDAR 
Command-->UserProgram: LiDAR Started successfully
UserProgram->LaserScan: Get Laser Scan Data
LaserScan-->UserProgram:  Laser Scan Data Recvied
note over UserProgram: doProcessSimple
loop Laser Scan Data
  LaserScan->UserProgram: doProcessSimple
end
note over UserProgram: TurnOff
UserProgram->Command: TurnOff 
note over UserProgram: disconnecting
UserProgram->Command: disconnecting
```

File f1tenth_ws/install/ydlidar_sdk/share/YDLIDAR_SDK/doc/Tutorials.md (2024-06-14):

# YDLIDAR SDK Tutorials

Non-Beginners: If you're already familiar enough with YDLIDAR SDK, you can go through more in-depth SDK tutorial here. However, going over all basic Beginner Level tutorials is still recommended for all users to get exposed to new features.

If you are new to Linux/windows: You may find it helpful to first do a quick tutorial on common command line tools for linux/windows. A good one is here. 

# Table of Contents
- [Beginner Level](#Beginner-level)
    - [Writing a Simple Lidar Turorial (C++)](#writing-a-simple-lidar-tutorial-(c++))
    - [Writing a Simple Lidar Network Adapter Turorial (C++)](#writing-a-simple-lidar-network-adapter-tutorial-(c++))
    - [Writing a Simple Lidar Turorial (Python)](#writing-a-simple-lidar-tutorial-(python))
    - [Writing a Simple Lidar Turorial (C)](#writing-a-simple-lidar-tutorial-(c))
    - [Examining the simple lidar tutorial](#examining-the-simple-lidar-tutorial)

## Beginner Level
### [Writing a Simple Lidar Tutorial (C++)](tutorials/writing_lidar_tutorial_c++.md)
This tutorial covers how to write a lidar tutorial in C++. 
### [Writing a Simple Lidar Network Adapter Tutorial (C++)](tutorials/writing_lidar_network_adapter_tutorial_c++.md)
This tutorial covers how to write a lidar network adapter tutorial in C++. 
### [Writing a Simple Lidar Tutorial (Python)](tutorials/writing_lidar_tutorial_python.md)
This tutorial covers how to write a lidar tutorial in Python. 
### [Writing a Simple Lidar Tutorial (C)](tutorials/writing_lidar_tutorial_c.md)
This tutorial covers how to write a lidar tutorial in C. 
### [Examining the simple lidar tutorial](tutorials/examine_the_simple_lidar_tutorial.md)
This tutorial examines running the lidar tutorial.

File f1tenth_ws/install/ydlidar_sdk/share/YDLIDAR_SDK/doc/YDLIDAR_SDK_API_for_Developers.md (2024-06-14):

# YDLIDAR SDK API for Developers

This document provides an extensive technical deep dive into how to create, manipulate and use YDLIDAR SDK's API.

## Table of Contents

- [Samples](#samples)
    - [Create A System State](#create-a-system-state)
    - [Code Example](#code-example)
    - [Python Example](#python)
- [ThridParty Project Call Library OR Source](#thridparty-project-call-library-or-source)
    - [Introduction](#introduction)
    - [Calling a compliled library](#calling-a-compliled-library).
    - [Add source code to the Project](#add-source-code-to-the-project).
- [Development Flow](#development-flow)
- [C++ API Directory](#api-directory)
    - [CYdLidar](#cydlidar-api)
    - [YDlidarDriver](#ydlidardriver-api)
    - [ETLidarDriver](#etlidardriver-api)
    - [Parameter Table](#parameter-table)

## Samples

The first part of demonstrating YDLIDAR SDK API is to understand the ydlidar_test/tof_test/etlidar_Test example. Following are one optinal concepts:  `ydlidar::os_init()` (basic unit) of the example.

### Create A System State 

In the YDLIDAR SDK, the `ydlidar::os_init()` is optinal unit, If you need to accept `Ctrl + C` or other system abnormal signals. you can use it to create a system state, and check whether the system is normal by `ydlidar::os_isOk()`.
The system signal creation interface is as follows:

```C
ydlidar::os_init();
```

-  when `ydlidar::os_init()` has called, the system is in an initialized state, able to accept `Ctrl + C` and `ydlidar::os_shutdown()` signals.

### Code Example

#### Triangle LiDAR (../samples/ydlidar_test.cpp)

```C
#include "CYdLidar.h"
#include <iostream>
#include <string>
#include <algorithm>
#include <cctype>
using namespace std;
using namespace ydlidar;
#if defined(_MSC_VER)
#pragma comment(lib, "ydlidar_sdk.lib")
#endif

int main(int argc, char *argv[]) {
  // init system signal
  ydlidar::os_init();

  CYdLidar laser;
  //////////////////////string property/////////////////
  /// lidar port
  std::string port = "/dev/ydlidar
  laser.setlidaropt(LidarPropSerialPort, port.c_str(), port.size());
  /// ignore array
  std::string ignore_array;
  ignore_array.clear();
  laser.setlidaropt(LidarPropIgnoreArray, ignore_array.c_str(),
                    ignore_array.size());

  //////////////////////int property/////////////////
  /// lidar baudrate
  int optval = 230400;
  laser.setlidaropt(LidarPropSerialBaudrate, &optval, sizeof(int));
  /// tof lidar
  int optval = TYPE_TRIANGLE;
  laser.setlidaropt(LidarPropLidarType, &optval, sizeof(int));
  /// device type
  optval = YDLIDAR_TYPE_SERIAL;
  laser.setlidaropt(LidarPropDeviceType, &optval, sizeof(int));
  /// sample rate
  optval = 9;
  laser.setlidaropt(LidarPropSampleRate, &optval, sizeof(int));
  /// abnormal count
  optval = 4;
  laser.setlidaropt(LidarPropAbnormalCheckCount, &optval, sizeof(int));

  //////////////////////bool property/////////////////
  /// fixed angle resolution
  bool b_optvalue = false;
  laser.setlidaropt(LidarPropFixedResolution, &b_optvalue, sizeof(bool));
  /// rotate 180
  laser.setlidaropt(LidarPropReversion, &b_optvalue, sizeof(bool));
  /// Counterclockwise
  laser.setlidaropt(LidarPropInverted, &b_optvalue, sizeof(bool));
  b_optvalue = true;
  laser.setlidaropt(LidarPropAutoReconnect, &b_optvalue, sizeof(bool));
  /// one-way communication
  b_optvalue = false;
  laser.setlidaropt(LidarPropSingleChannel, &b_optvalue, sizeof(bool));
  /// intensity
  b_optvalue = false;
  laser.setlidaropt(LidarPropIntenstiy, &b_optvalue, sizeof(bool));
  /// Motor DTR
  b_optvalue = false;
  laser.setlidaropt(LidarPropSupportMotorDtrCtrl, &b_optvalue, sizeof(bool));

  //////////////////////float property/////////////////
  /// unit: °
  float f_optvalue = 180.0f;
  laser.setlidaropt(LidarPropMaxAngle, &f_optvalue, sizeof(float));
  f_optvalue = -180.0f;
  laser.setlidaropt(LidarPropMinAngle, &f_optvalue, sizeof(float));
  /// unit: m
  f_optvalue = 16.f;
  laser.setlidaropt(LidarPropMaxRange, &f_optvalue, sizeof(float));
  f_optvalue = 0.1f;
  laser.setlidaropt(LidarPropMinRange, &f_optvalue, sizeof(float));
  /// unit: Hz
  f_optvalue = 10.f;
  laser.setlidaropt(LidarPropScanFrequency, &f_optvalue, sizeof(float));

  // initialize SDK and LiDAR
  bool ret = laser.initialize();
  if (ret) {//success
    //Start the device scanning routine which runs on a separate thread and enable motor.
    ret = laser.turnOn();
  } else {
    fprintf(stderr, "%s\n", laser.DescribeError());
    fflush(stderr);
  }

  // Turn On success and loop  
  while (ret && ydlidar::os_isOk()) {
    LaserScan scan;
    if (laser.doProcessSimple(scan)) {
      fprintf(stdout, "Scan received[%llu]: %u ranges is [%f]Hz\n",
              scan.stamp,
              (unsigned int)scan.points.size(), 1.0 / scan.config.scan_time);
      fflush(stdout);
    } else {
      fprintf(stderr, "Failed to get Lidar Data\n");
      fflush(stderr);
    }
  }
  // Stop the device scanning thread and disable motor.
  laser.turnOff();
  // Uninitialize the SDK and Disconnect the LiDAR.
  laser.disconnecting();
  return 0;
}
```

#### TOF LiDAR (../samples/tof_test.cpp)

```C
#include "CYdLidar.h"
#include <iostream>
#include <string>
#include <algorithm>
#include <cctype>
using namespace std;
using namespace ydlidar;
#if defined(_MSC_VER)
#pragma comment(lib, "ydlidar_sdk.lib")
#endif

int main(int argc, char *argv[]) {
  // init system signal
  ydlidar::os_init();

  CYdLidar laser;
  //////////////////////string property/////////////////
  /// lidar port
  std::string port = "/dev/ydlidar
  laser.setlidaropt(LidarPropSerialPort, port.c_str(), port.size());
  /// ignore array
  std::string ignore_array;
  ignore_array.clear();
  laser.setlidaropt(LidarPropIgnoreArray, ignore_array.c_str(),
                    ignore_array.size());

  //////////////////////int property/////////////////
  /// lidar baudrate
  int optval = 512000;
  laser.setlidaropt(LidarPropSerialBaudrate, &optval, sizeof(int));
  /// tof lidar
  int optval = TYPE_TOF;
  laser.setlidaropt(LidarPropLidarType, &optval, sizeof(int));
  /// device type
  optval = YDLIDAR_TYPE_SERIAL;
  laser.setlidaropt(LidarPropDeviceType, &optval, sizeof(int));
  /// sample rate
  optval = 20;
  laser.setlidaropt(LidarPropSampleRate, &optval, sizeof(int));
  /// abnormal count
  optval = 4;
  laser.setlidaropt(LidarPropAbnormalCheckCount, &optval, sizeof(int));

  //////////////////////bool property/////////////////
  /// fixed angle resolution
  bool b_optvalue = false;
  laser.setlidaropt(LidarPropFixedResolution, &b_optvalue, sizeof(bool));
  /// rotate 180
  laser.setlidaropt(LidarPropReversion, &b_optvalue, sizeof(bool));
  /// Counterclockwise
  laser.setlidaropt(LidarPropInverted, &b_optvalue, sizeof(bool));
  b_optvalue = true;
  laser.setlidaropt(LidarPropAutoReconnect, &b_optvalue, sizeof(bool));
  /// one-way communication
  b_optvalue = false;
  laser.setlidaropt(LidarPropSingleChannel, &b_optvalue, sizeof(bool));
  /// intensity
  b_optvalue = false;
  laser.setlidaropt(LidarPropIntenstiy, &b_optvalue, sizeof(bool));
  /// Motor DTR
  b_optvalue = false;
  laser.setlidaropt(LidarPropSupportMotorDtrCtrl, &b_optvalue, sizeof(bool));

  //////////////////////float property/////////////////
  /// unit: °
  float f_optvalue = 180.0f;
  laser.setlidaropt(LidarPropMaxAngle, &f_optvalue, sizeof(float));
  f_optvalue = -180.0f;
  laser.setlidaropt(LidarPropMinAngle, &f_optvalue, sizeof(float));
  /// unit: m
  f_optvalue = 64.f;
  laser.setlidaropt(LidarPropMaxRange, &f_optvalue, sizeof(float));
  f_optvalue = 0.05f;
  laser.setlidaropt(LidarPropMinRange, &f_optvalue, sizeof(float));
  /// unit: Hz
  f_optvalue = 10.f;
  laser.setlidaropt(LidarPropScanFrequency, &f_optvalue, sizeof(float));

  // initialize SDK and LiDAR
  bool ret = laser.initialize();
  if (ret) {//success
    //Start the device scanning routine which runs on a separate thread and enable motor.
    ret = laser.turnOn();
  } else {
    fprintf(stderr, "%s\n", laser.DescribeError());
    fflush(stderr);
  }

  // Turn On success and loop  
  while (ret && ydlidar::os_isOk()) {
    LaserScan scan;
    if (laser.doProcessSimple(scan)) {
      fprintf(stdout, "Scan received[%llu]: %u ranges is [%f]Hz\n",
              scan.stamp,
              (unsigned int)scan.points.size(), 1.0 / scan.config.scan_time);
      fflush(stdout);
    } else {
      fprintf(stderr, "Failed to get Lidar Data\n");
      fflush(stderr);
    }
  }
  // Stop the device scanning thread and disable motor.
  laser.turnOff();
  // Uninitialize the SDK and Disconnect the LiDAR.
  laser.disconnecting();
  return 0;
}
```

#### CMake BUILD file(../samples/CMakeLists.txt)
```cmake
cmake_minimum_required(VERSION 2.8)
PROJECT(ydlidar_test)
set(CMAKE_CXX_FLAGS "${CMAKE_CXX_FLAGS} -std=c++11")
add_definitions(-std=c++11) # Use C++11

#Include directories
INCLUDE_DIRECTORIES(
     ${CMAKE_SOURCE_DIR}
     ${CMAKE_SOURCE_DIR}/../
     ${CMAKE_CURRENT_BINARY_DIR}
)

SET(EXECUTABLE_OUTPUT_PATH ${CMAKE_BINARY_DIR})

set(curdir ${CMAKE_CURRENT_SOURCE_DIR})
FILE(GLOB APP_LIST "${curdir}/*.cpp")
foreach(child ${APP_LIST})
  string(REPLACE "${curdir}/" "" app_main ${child})
  string(REPLACE ".cpp" "" APP_NAME ${app_main})
  ADD_EXECUTABLE(${APP_NAME} ${app_main})
  TARGET_LINK_LIBRARIES(${APP_NAME} ydlidar_sdk)
endforeach()
```
#### Build and Run
- Build: cd build & cmake ../ & make
- Run ydlidar_test or tof_test in terminals:
	- ./ydlidar_test
	- ./tof_test
- Examine the results: you should see message printing out in terminals.

### Python
```python
import os
import ydlidar
import time

if __name__ == "__main__":
    ydlidar.os_init();
    laser = ydlidar.CYdLidar();
    laser.setlidaropt(ydlidar.LidarPropSerialPort, "/dev/ydlidar");
    laser.setlidaropt(ydlidar.LidarPropSerialBaudrate, 230400);
    laser.setlidaropt(ydlidar.LidarPropLidarType, ydlidar.TYPE_TRIANGLE);
    laser.setlidaropt(ydlidar.LidarPropDeviceType, ydlidar.YDLIDAR_TYPE_SERIAL);
    laser.setlidaropt(ydlidar.LidarPropScanFrequency, 10.0);
    laser.setlidaropt(ydlidar.LidarPropSampleRate, 9);
    laser.setlidaropt(ydlidar.LidarPropSingleChannel, False);

    ret = laser.initialize();
    if ret:
        ret = laser.turnOn();
        scan = ydlidar.LaserScan();
        while ret and ydlidar.os_isOk() :
            r = laser.doProcessSimple(scan);
            if r:
                print("Scan received[",scan.stamp,"]:",scan.points.size(),"ranges is [",1.0/scan.config.scan_time,"]Hz");
            else :
                print("Failed to get Lidar Data")
            time.sleep(0.05);
        laser.turnOff();
    laser.disconnecting();

```

## ThridParty Project Call Library OR Source

### Introduction

There are two ways to integrate YDLIDAR SDK into your project.
* [Calling a compliled library](#calling-a-compliled-library).
    - [Download YDLIDAR SDK](#download-ydlidar-sdk)
    - [Build and Install](#build-and-install)
    - [Add YDLIDAR SDK to the CMakeLists file of your project](#add-ydlidar-sdk-to-the-cmakelists-file-of-your-project)
* [Add source code to the Project](#add-source-code-to-the-project).
    - [Copy YDLIDAR SDK to your project](#copy-ydlidar-sdk-to-your-project)
    - [Add YDLIDAR SDK project to the CMakeLists file of your project](#add-ydlidar-sdk-project-to-the-cmakelists-file-of-your-project)

### Calling a compliled library
The implementation of the demo mainly includes the following steps.

#### Download YDLIDAR SDK
```shell
$git clone https://github.com/YDLIDAR/YDLidar-SDK
```
#### Build and Install
```shell
$cd YDLidar-SDK/build
$cmake ../
$make
$sudo make install
```
Note:
* Default generate static library.
* If you want to generate YDLidar-SDK dynamic library, Add the following options when compiling:
```shell
$cmake -DBUILD_SHARED_LIBS=ON ../ && make
```

#### Add YDLIDAR SDK to the CMakeLists file of your project
```cmake
############## YDLIDAR SDK START#####################################
#find ydlidar_sdk package
find_package(ydlidar_sdk)
#Include directories
INCLUDE_DIRECTORIES(
  ${YDLIDAR_SDK_INCLUDE_DIRS}
)
#link library directories
link_directories(${YDLIDAR_SDK_LIBRARY_DIRS})

#Link your project to ydlidar_sdk library.
target_link_libraries(${PROJECT_NAME} ${YDLIDAR_SDK_LIBRARIES})

############## YDLIDAR SDK END#####################################
```

Detailed call Demo, see [here](https://github.com/YDLIDAR/ydlidar_tutorials)

### Add source code to the Project
The implementation of the demo mainly includes the following steps.

#### Copy YDLIDAR SDK to your project
```shell
$cd 'your project'
$git clone https://github.com/YDLIDAR/YDLidar-SDK
```
Note: The same can be downloaded and placed in your project directory.

#### Add YDLIDAR SDK project to the CMakeLists file of your project
```cmake
############## YDLIDAR SDK START#####################################
#Include directories
INCLUDE_DIRECTORIES(
  ${CMAKE_SOURCE_DIR}
  ${CMAKE_SOURCE_DIR}/YDLidar-SDK
  ${CMAKE_SOURCE_DIR}/YDLidar-SDK/src
  ${CMAKE_CURRENT_BINARY_DIR}/YDLidar-SDK
)
#Add YDLIDAR SDK sub project
add_subdirectory(YDLidar-SDK)

#Link your project to ydlidar_sdk library.
target_link_libraries(${PROJECT_NAME} ydlidar_sdk)

############## YDLIDAR SDK END#####################################
```
Note: 
* If you do not want to generate samples in YDLidar-SDK, Add the following options when compiling:
```shell
$cmake -DBUILD_EXAMPLES=OFF ../ && make
```
* If you want to generate YDLidar-SDK dynamic library, Add the following options when compiling:
```shell
$cmake -DBUILD_SHARED_LIBS=ON ../ && make
```
* If you want to meet both of the above conditions, the operation is as follows:
```shell
$cmake -DBUILD_EXAMPLES=OFF -DBUILD_SHARED_LIBS=ON ../ && make
```
Detailed call Demo, see [here](https://github.com/YDLIDAR/DemoProject/YDLidar-SDK-Source-Demo)

## Development Flow

### FlowChart
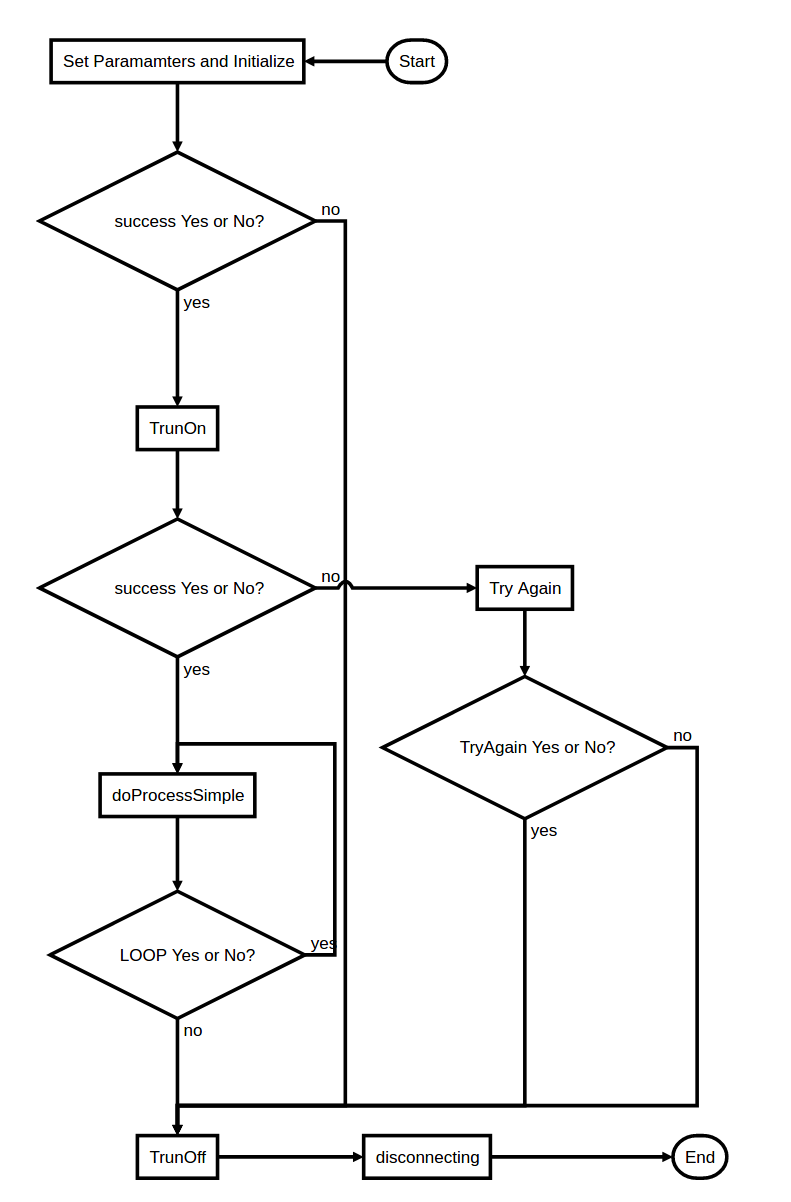
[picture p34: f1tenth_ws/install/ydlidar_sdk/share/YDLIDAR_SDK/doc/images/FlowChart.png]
Development FlowChart


### Sequence
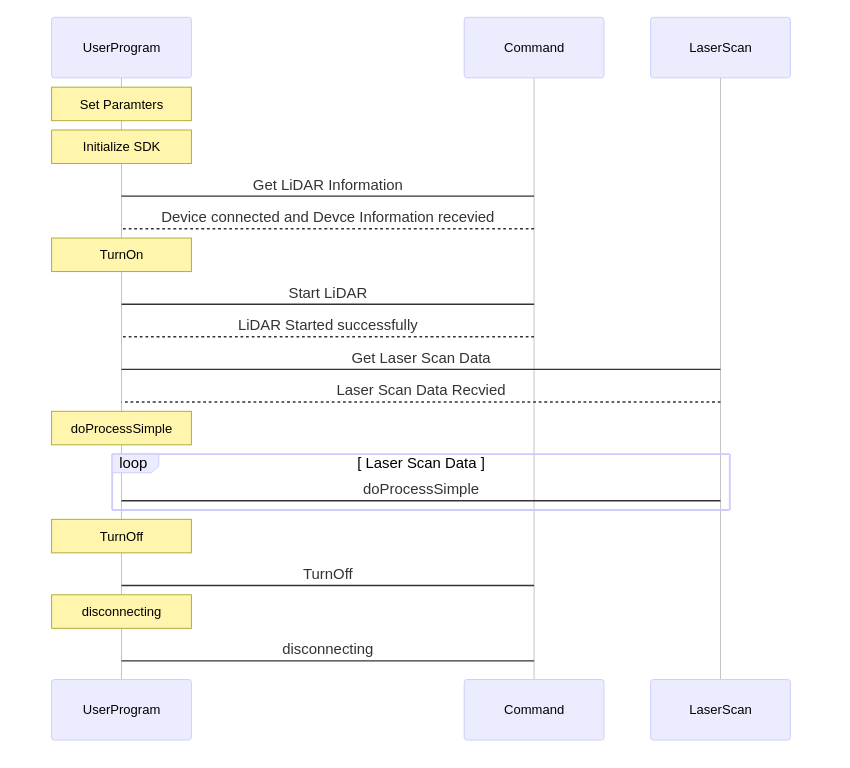
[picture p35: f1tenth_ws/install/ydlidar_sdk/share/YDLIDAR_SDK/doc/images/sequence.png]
Development sequenceDiagram


## API Directory

### CYDLidar API
For additional information and examples, refer to [CYDLidar](#cydlidar)

### API List

#### C++ API

```C++
/**
* @brief set lidar properties
* @param optname        option name
* @todo string properties
* - @ref LidarPropSerialPort
* - @ref LidarPropIgnoreArray
* @note set string property example
* @code
* CYdLidar laser;
* std::string lidar_port = "/dev/ydlidar";
* laser.setlidaropt(LidarPropSerialPort,lidar_port.c_str(), lidar_port.size());
* @endcode
* @todo int properties
* - @ref LidarPropSerialBaudrate
* - @ref LidarPropLidarType
* - @ref LidarPropDeviceType
* - @ref LidarPropSampleRate
* @note set int property example
* @code
* CYdLidar laser;
* int lidar_baudrate = 230400;
* laser.setlidaropt(LidarPropSerialPort,&lidar_baudrate, sizeof(int));
* @endcode
* @todo bool properties
* - @ref LidarPropFixedResolution
* - @ref LidarPropReversion
* - @ref LidarPropInverted
* - @ref LidarPropAutoReconnect
* - @ref LidarPropSingleChannel
* - @ref LidarPropIntenstiy
* - @ref LidarPropSupportMotorDtrCtrl
* - @ref LidarPropSupportHeartBeat
* @note set bool property example
* @code
* CYdLidar laser;
* bool lidar_fixedresolution = true;
* laser.setlidaropt(LidarPropSerialPort,&lidar_fixedresolution, sizeof(bool));
* @endcode
* @todo float properties
* - @ref LidarPropMaxRange
* - @ref LidarPropMinRange
* - @ref LidarPropMaxAngle
* - @ref LidarPropMinAngle
* - @ref LidarPropScanFrequency
* @note set float property example
* @code
* CYdLidar laser;
* float lidar_maxrange = 16.0f;
* laser.setlidaropt(LidarPropSerialPort,&lidar_maxrange, sizeof(float));
* @endcode
* @param optval         option value
* - std::string(or char*)
* - int
* - bool
* - float
* @param optlen         option length
* - data type size
* @return true if the Property is set successfully, otherwise false.
* @see LidarProperty
*/
bool setlidaropt(int optname, const void *optval, int optlen);

/**
* @brief get lidar property
* @param optname         option name
* @todo string properties
* - @ref LidarPropSerialPort
* - @ref LidarPropIgnoreArray
* @note get string property example
* @code
* CYdLidar laser;
* char lidar_port[30];
* laser.getlidaropt(LidarPropSerialPort,lidar_port, sizeof(lidar_port));
* @endcode
* @todo int properties
* - @ref LidarPropSerialBaudrate
* - @ref LidarPropLidarType
* - @ref LidarPropDeviceType
* - @ref LidarPropSampleRate
* @note get int property example
* @code
* CYdLidar laser;
* int lidar_baudrate;
* laser.getlidaropt(LidarPropSerialPort,&lidar_baudrate, sizeof(int));
* @endcode
* @todo bool properties
* - @ref LidarPropFixedResolution
* - @ref LidarPropReversion
* - @ref LidarPropInverted
* - @ref LidarPropAutoReconnect
* - @ref LidarPropSingleChannel
* - @ref LidarPropIntenstiy
* - @ref LidarPropSupportMotorDtrCtrl
* - @ref LidarPropSupportHeartBeat
* @note get bool property example
* @code
* CYdLidar laser;
* bool lidar_fixedresolution;
* laser.getlidaropt(LidarPropSerialPort,&lidar_fixedresolution, sizeof(bool));
* @endcode
* @todo float properties
* - @ref LidarPropMaxRange
* - @ref LidarPropMinRange
* - @ref LidarPropMaxAngle
* - @ref LidarPropMinAngle
* - @ref LidarPropScanFrequency
* @note set float property example
* @code
* CYdLidar laser;
* float lidar_maxrange;
* laser.getlidaropt(LidarPropSerialPort,&lidar_maxrange, sizeof(float));
* @endcode
* @param optval          option value
* - std::string(or char*)
* - int
* - bool
* - float
* @param optlen          option length
* - data type size
* @return true if the Property is get successfully, otherwise false.
* @see LidarProperty
*/
bool getlidaropt(int optname, void *optval, int optlen);
/**
 * @brief Initialize the SDK and LiDAR.
 * @return true if successfully initialized, otherwise false.
 */
bool initialize();

/**
* @brief Return LiDAR's version information in a numeric form.
* @param version Pointer to a version structure for returning the version information.
*/
void GetLidarVersion(LidarVersion &version);

/**
 * @brief Start the device scanning routine which runs on a separate thread and enable motor.
 * @return true if successfully started, otherwise false.
 */
bool  turnOn();
/**
 * @brief Get the LiDAR Scan Data. turnOn is successful before doProcessSimple scan data.
 * @param[out] outscan             LiDAR Scan Data
 * @param[out] hardwareError       hardware error status
 * @return true if successfully started, otherwise false.
 */
bool doProcessSimple(LaserScan &outscan, bool &hardwareError);
/**
 * @brief Stop the device scanning thread and disable motor.
 * @return true if successfully Stoped, otherwise false.
 */
bool  turnOff();
/**
 * @brief Uninitialize the SDK and Disconnect the LiDAR.
 */
void disconnecting();

/**
 * @brief Get the last error information of a (socket or serial)
 * @return a human-readable description of the given error information
 * or the last error information of a (socket or serial)
 */
const char *DescribeError() const;
```
#### C API
```C
/**
 * @brief create a Lidar instance
 * @note call ::lidarDestroy destroy
 * @return created instance
 */
YDLidar *lidarCreate(void);

/**
 * @brief Destroy Lidar instance by ::lidarCreate create
 * @param lidar     CYdLidar instance
 */
void lidarDestroy(YDLidar **lidar);

/**
 * @brief set lidar properties
 * @param lidar           a lidar instance
 * @param optname        option name
 * @todo string properties
 * - @ref LidarPropSerialPort
 * - @ref LidarPropIgnoreArray
 * @note set string property example
 * @code
 * CYdLidar laser;
 * std::string lidar_port = "/dev/ydlidar";
 * laser.setlidaropt(LidarPropSerialPort,lidar_port.c_str(), lidar_port.size());
 * @endcode
 * @todo int properties
 * - @ref LidarPropSerialBaudrate
 * - @ref LidarPropLidarType
 * - @ref LidarPropDeviceType
 * - @ref LidarPropSampleRate
 * @note set int property example
 * @code
 * CYdLidar laser;
 * int lidar_baudrate = 230400;
 * laser.setlidaropt(LidarPropSerialPort,&lidar_baudrate, sizeof(int));
 * @endcode
 * @todo bool properties
 * - @ref LidarPropFixedResolution
 * - @ref LidarPropReversion
 * - @ref LidarPropInverted
 * - @ref LidarPropAutoReconnect
 * - @ref LidarPropSingleChannel
 * - @ref LidarPropIntenstiy
 * - @ref LidarPropSupportMotorDtrCtrl
 * - @ref LidarPropSupportHeartBeat
 * @note set bool property example
 * @code
 * CYdLidar laser;
 * bool lidar_fixedresolution = true;
 * laser.setlidaropt(LidarPropSerialPort,&lidar_fixedresolution, sizeof(bool));
 * @endcode
 * @todo float properties
 * - @ref LidarPropMaxRange
 * - @ref LidarPropMinRange
 * - @ref LidarPropMaxAngle
 * - @ref LidarPropMinAngle
 * - @ref LidarPropScanFrequency
 * @note set float property example
 * @code
 * CYdLidar laser;
 * float lidar_maxrange = 16.0f;
 * laser.setlidaropt(LidarPropSerialPort,&lidar_maxrange, sizeof(float));
 * @endcode
 * @param optval         option value
 * - std::string(or char*)
 * - int
 * - bool
 * - float
 * @param optlen         option length
 * - data type size
 * @return true if the Property is set successfully, otherwise false.
 * @see LidarProperty
 */
bool setlidaropt(YDLidar *lidar, int optname, const void *optval, int optlen);

/**
 * @brief get lidar property
 * @param lidar           a lidar instance
 * @param optname         option name
 * @todo string properties
 * - @ref LidarPropSerialPort
 * - @ref LidarPropIgnoreArray
 * @note get string property example
 * @code
 * CYdLidar laser;
 * char lidar_port[30];
 * laser.getlidaropt(LidarPropSerialPort,lidar_port, sizeof(lidar_port));
 * @endcode
 * @todo int properties
 * - @ref LidarPropSerialBaudrate
 * - @ref LidarPropLidarType
 * - @ref LidarPropDeviceType
 * - @ref LidarPropSampleRate
 * @note get int property example
 * @code
 * CYdLidar laser;
 * int lidar_baudrate;
 * laser.getlidaropt(LidarPropSerialPort,&lidar_baudrate, sizeof(int));
 * @endcode
 * @todo bool properties
 * - @ref LidarPropFixedResolution
 * - @ref LidarPropReversion
 * - @ref LidarPropInverted
 * - @ref LidarPropAutoReconnect
 * - @ref LidarPropSingleChannel
 * - @ref LidarPropIntenstiy
 * - @ref LidarPropSupportMotorDtrCtrl
 * - @ref LidarPropSupportHeartBeat
 * @note get bool property example
 * @code
 * CYdLidar laser;
 * bool lidar_fixedresolution;
 * laser.getlidaropt(LidarPropSerialPort,&lidar_fixedresolution, sizeof(bool));
 * @endcode
 * @todo float properties
 * - @ref LidarPropMaxRange
 * - @ref LidarPropMinRange
 * - @ref LidarPropMaxAngle
 * - @ref LidarPropMinAngle
 * - @ref LidarPropScanFrequency
 * @note set float property example
 * @code
 * CYdLidar laser;
 * float lidar_maxrange;
 * laser.getlidaropt(LidarPropSerialPort,&lidar_maxrange, sizeof(float));
 * @endcode
 * @param optval          option value
 * - std::string(or char*)
 * - int
 * - bool
 * - float
 * @param optlen          option length
 * - data type size
 * @return true if the Property is get successfully, otherwise false.
 * @see LidarProperty
 */
bool getlidaropt(YDLidar *lidar, int optname, void *optval, int optlen);

/**
* Return SDK's version information in a numeric form.
* @param version Pointer to a version for returning the version information.
*/
void GetSdkVersion(char *version);

/**
 * Initialize the SDK.
 * @return true if successfully initialized, otherwise false.
 */
bool initialize(YDLidar *lidar);

/**
* @brief Return LiDAR's version information in a numeric form.
* @param version Pointer to a version structure for returning the version information.
*/
void GetLidarVersion(YDLidar *lidar, LidarVersion *version);

/**
 * Start the device scanning routine which runs on a separate thread.
 * @return true if successfully started, otherwise false.
 */
bool turnOn(YDLidar *lidar);

/**
 * @brief Get the LiDAR Scan Data. turnOn is successful before doProcessSimple scan data.
 * @param[in] lidar          LiDAR instance
 * @param[out] outscan       LiDAR Scan Data
 * @return true if successfully started, otherwise false.
 */
bool doProcessSimple(YDLidar *lidar, LaserFan *outscan);
/**
 * @brief Stop the device scanning thread and disable motor.
 * @return true if successfully Stoped, otherwise false.
 */
bool  turnOff(YDLidar *lidar);
/**
 * @brief Uninitialize the SDK and Disconnect the LiDAR.
 */
void disconnecting(YDLidar *lidar);

/**
 * @brief Get the last error information of a (socket or serial)
 * @return a human-readable description of the given error information
 * or the last error information of a (socket or serial)
 */
const char *DescribeError(YDLidar *lidar);

/**
 * @brief initialize system signals
 */
void os_init();
/**
 * @brief isOk
 * @return true if successfully initialize, otherwise false.
 */
bool os_isOk();
/**
 * @brief os_shutdown
 */
void os_shutdown();

/**
 * @brief get lidar serial port
 * @param ports serial port lists
 * @return valid port number
 */
int lidarPortList(LidarPort *ports);

```

## YDlidarDriver API
For additional information and examples, refer to [YDlidarDriver](../src/ydlidar_driver.h)

### API List

```C
  /**
   * @brief Connecting Lidar \n
   * After the connection if successful, you must use ::disconnect to close
   * @param[in] port_path    serial port
   * @param[in] baudrate    serial baudrate，YDLIDAR-SS：
   *     230400 G2-SS-1 R2-SS-1
   * @return connection status
   * @retval 0     success
   * @retval < 0   failed
   * @note After the connection if successful, you must use ::disconnect to close
   * @see function ::YDlidarDriver::disconnect ()
   */
  virtual result_t connect(const char *port_path, uint32_t baudrate);

  /**
   * @brief Returns a human-readable description of the given error code
   *  or the last error code of a socket or serial port
   * @param isTCP   TCP or UDP
   * @return error information
   */
  virtual const char *DescribeError(bool isTCP = true);

  /*!
  * @brief Disconnect the LiDAR.
  */
  virtual void disconnect();

  /**
  * @brief Get SDK Version \n
  * static function
  * @return Version
  */
  virtual std::string getSDKVersion();

  /**
   * @brief lidarPortList Get Lidar Port lists
   * @return online lidars
   */
  static std::map<std::string, std::string> lidarPortList();

  /**
   * @brief Is the Lidar in the scan \n
   * @return scanning status
   * @retval true     scanning
   * @retval false    non-scanning
   */
  virtual bool isscanning() const;

  /**
   * @brief Is it connected to the lidar \n
   * @return connection status
   * @retval true     connected
   * @retval false    Non-connected
   */
  virtual bool isconnected() const;

  /**
   * @brief Is there intensity \n
   * @param[in] isintensities    intentsity
   *   true	intensity
   *   false no intensity
   */
  virtual void setIntensities(const bool &isintensities);

  /**
   * @brief whether to support hot plug \n
   * @param[in] enable    hot plug :
   *   true	support
   *   false no support
   */
  virtual void setAutoReconnect(const bool &enable);

  /**
   * @brief get Health status \n
   * @return result status
   * @retval RESULT_OK       success
   * @retval RESULT_FAILE or RESULT_TIMEOUT   failed
   */
  virtual result_t getHealth(device_health &health,
                             uint32_t timeout = DEFAULT_TIMEOUT);

  /**
   * @brief get Device information \n
   * @param[in] info     Device information
   * @param[in] timeout  timeout
   * @return result status
   * @retval RESULT_OK       success
   * @retval RESULT_FAILE or RESULT_TIMEOUT   failed
   */
  virtual result_t getDeviceInfo(device_info &info,
                                 uint32_t timeout = DEFAULT_TIMEOUT);

  /**
   * @brief Turn on scanning \n
   * @param[in] force    Scan mode
   * @param[in] timeout  timeout
   * @return result status
   * @retval RESULT_OK       success
   * @retval RESULT_FAILE    failed
   * @note Just turn it on once
   */
  virtual result_t startScan(bool force = false,
                             uint32_t timeout = DEFAULT_TIMEOUT) ;

  /**
   * @brief turn off scanning \n
   * @return result status
   * @retval RESULT_OK       success
   * @retval RESULT_FAILE    failed
   */
  virtual result_t stop();

  /**
   * @brief Get a circle of laser data \n
   * @param[in] nodebuffer Laser data
   * @param[in] count      one circle of laser points
   * @param[in] timeout    timeout
   * @return return status
   * @retval RESULT_OK       success
   * @retval RESULT_FAILE    failed
   * @note Before starting, you must start the start the scan successfully with the ::startScan function
   */
  virtual result_t grabScanData(node_info *nodebuffer, size_t &count,
                                uint32_t timeout = DEFAULT_TIMEOUT) ;

  /**
   * @brief Normalized angle \n
   * Normalize the angel between 0 and 360
   * @param[in] nodebuffer Laser data
   * @param[in] count      one circle of laser points
   * @return return status
   * @retval RESULT_OK       success
   * @retval RESULT_FAILE    failed
   * @note Before the normalization, you must use the ::grabScanData function to get the laser data successfully.
   */
  result_t ascendScanData(node_info *nodebuffer, size_t count);

  /**
  * @brief reset lidar \n
  * @param[in] timeout      timeout
  * @return return status
  * @retval RESULT_OK       success
  * @retval RESULT_FAILE    failed
  * @note Non-scan state, perform currect operation.
  */
  result_t reset(uint32_t timeout = DEFAULT_TIMEOUT);

  /**
   * @brief start motor \n
   * @return return status
   * @retval RESULT_OK       success
   * @retval RESULT_FAILE    failed
   */
  result_t startMotor();

  /**
   * @brief stop motor \n
   * @return return status
   * @retval RESULT_OK       success
   * @retval RESULT_FAILE    failed
   */
  result_t stopMotor();

  /**
  * @brief Get lidar scan frequency \n
  * @param[in] frequency    scanning frequency
  * @param[in] timeout      timeout
  * @return return status
  * @retval RESULT_OK       success
  * @retval RESULT_FAILE    failed
  * @note Non-scan state, perform currect operation.
  */
  virtual  result_t getScanFrequency(scan_frequency &frequency,
                                     uint32_t timeout = DEFAULT_TIMEOUT);

  /**
   * @brief Increase the scanning frequency by 1.0 HZ \n
   * @param[in] frequency    scanning frequency
   * @param[in] timeout      timeout
   * @return return status
   * @retval RESULT_OK       success
   * @retval RESULT_FAILE    failed
   * @note Non-scan state, perform currect operation.
   */
  virtual result_t setScanFrequencyAdd(scan_frequency &frequency,
                                       uint32_t timeout = DEFAULT_TIMEOUT);

  /**
   * @brief Reduce the scanning frequency by 1.0 HZ \n
   * @param[in] frequency    scanning frequency
   * @param[in] timeout      timeout
   * @return return status
   * @retval RESULT_OK       success
   * @retval RESULT_FAILE    failed
   * @note Non-scan state, perform currect operation.
   */
  virtual result_t setScanFrequencyDis(scan_frequency &frequency,
                                       uint32_t timeout = DEFAULT_TIMEOUT);

  /**
   * @brief Increase the scanning frequency by 0.1 HZ \n
   * @param[in] frequency    scanning frequency
   * @param[in] timeout      timeout
   * @return return status
   * @retval RESULT_OK       success
   * @retval RESULT_FAILE    failed
   * @note Non-scan state, perform currect operation.
   */
  virtual result_t setScanFrequencyAddMic(scan_frequency &frequency,
                                          uint32_t timeout = DEFAULT_TIMEOUT);

  /**
   * @brief Reduce the scanning frequency by 0.1 HZ \n
   * @param[in] frequency    scanning frequency
   * @param[in] timeout      timeout
   * @return return status
   * @retval RESULT_OK       success
   * @retval RESULT_FAILE    failed
   * @note Non-scan state, perform currect operation.
   */
  virtual result_t setScanFrequencyDisMic(scan_frequency &frequency,
                                          uint32_t timeout = DEFAULT_TIMEOUT);

  /**
   * @brief Get lidar sampling frequency \n
   * @param[in] frequency    sampling frequency
   * @param[in] timeout      timeout
   * @return return status
   * @retval RESULT_OK       success
   * @retval RESULT_FAILE    failed
   * @note Non-scan state, perform currect operation.
   */
  virtual result_t getSamplingRate(sampling_rate &rate,
                                   uint32_t timeout = DEFAULT_TIMEOUT);

  /**
   * @brief Set the lidar sampling frequency \n
   * @param[in] rate    　　　sampling frequency
   * @param[in] timeout      timeout
   * @return return status
   * @retval RESULT_OK       success
   * @retval RESULT_FAILE    failed
   * @note Non-scan state, perform currect operation.
   */
  virtual result_t setSamplingRate(sampling_rate &rate,
                                   uint32_t timeout = DEFAULT_TIMEOUT);

  /**
   * @brief get lidar zero offset angle \n
   * @param[in] angle　　　   zero offset angle
   * @param[in] timeout      timeout
   * @return return status
   * @retval RESULT_OK       success
   * @retval RESULT_FAILE    failed
   * @note Non-scan state, perform currect operation.
   */
  virtual result_t getZeroOffsetAngle(offset_angle &angle,
                                      uint32_t timeout = DEFAULT_TIMEOUT);
```

## ETLidarDriver API
For additional information and examples, refer to [ETLidarDriver](../src/ETLidarDriver.h)

### API List

```C
  /**
   * @brief Connecting Lidar \n
   * After the connection if successful, you must use ::disconnect to close
   * @param[in] port_path    Ip Address
   * @param[in] baudrate     network port
   * @return connection status
   * @retval 0     success
   * @retval < 0   failed
   * @note After the connection if successful, you must use ::disconnect to close
   * @see function ::YDlidarDriver::disconnect ()
   */
  virtual result_t connect(const char *port_path, uint32_t baudrate = 8000);

  /**
   * @brief Returns a human-readable description of the given error code
   *  or the last error code of a socket
   * @param isTCP   TCP or UDP
   * @return error information
   */
  virtual const char *DescribeError(bool isTCP = true);

  /**
  * @brief Disconnect from ETLidar device.
  */
  virtual void disconnect();

  /**
  * @brief Get SDK Version
  * @return version
  */
  virtual std::string getSDKVersion();

  /**
   * @brief Is the Lidar in the scan \n
   * @return scanning status
   * @retval true     scanning
   * @retval false    non-scanning
   */
  virtual bool isscanning() const;

  /**
   * @brief Is it connected to the lidar \n
   * @return connection status
   * @retval true     connected
   * @retval false    Non-connected
   */
  virtual bool isconnected() const;

  /**
   * @brief Is there intensity \n
   * @param[in] isintensities    intentsity
   *   true	intensity
   *   false no intensity
   */
  virtual void setIntensities(const bool &isintensities);

  /**
   * @brief whether to support hot plug \n
   * @param[in] enable    hot plug :
   *   true	support
   *   false no support
   */
  virtual void setAutoReconnect(const bool &enable);

  /**
   * @brief get Health status \n
   * @return result status
   * @retval RESULT_OK       success
   * @retval RESULT_FAILE or RESULT_TIMEOUT   failed
   */
  virtual result_t getHealth(device_health &health,
                             uint32_t timeout = DEFAULT_TIMEOUT);

  /**
   * @brief get Device information \n
   * @param[in] info     Device information
   * @param[in] timeout  timeout
   * @return result status
   * @retval RESULT_OK       success
   * @retval RESULT_FAILE or RESULT_TIMEOUT   failed
   */
  virtual result_t getDeviceInfo(device_info &info,
                                 uint32_t timeout = DEFAULT_TIMEOUT);

  /**
   * @brief Turn on scanning \n
   * @param[in] force    Scan mode
   * @param[in] timeout  timeout
   * @return result status
   * @retval RESULT_OK       success
   * @retval RESULT_FAILE    failed
   * @note Just turn it on once
   */
  virtual result_t startScan(bool force = false,
                             uint32_t timeout = DEFAULT_TIMEOUT) ;

  /**
   * @brief turn off scanning \n
   * @return result status
   * @retval RESULT_OK       success
   * @retval RESULT_FAILE    failed
   */
  virtual result_t stop();

  /**
   * @brief Get a circle of laser data \n
   * @param[in] nodebuffer Laser data
   * @param[in] count      one circle of laser points
   * @param[in] timeout    timeout
   * @return return status
   * @retval RESULT_OK       success
   * @retval RESULT_FAILE    failed
   * @note Before starting, you must start the start the scan successfully with the ::startScan function
   */
  virtual result_t grabScanData(node_info *nodebuffer, size_t &count,
                                uint32_t timeout = DEFAULT_TIMEOUT) ;

  /**
   * @brief Get lidar scan frequency \n
   * @param[in] frequency    scanning frequency
   * @param[in] timeout      timeout
   * @return return status
   * @retval RESULT_OK       success
   * @retval RESULT_FAILE    failed
   * @note Non-scan state, perform currect operation.
   */
  virtual result_t getScanFrequency(scan_frequency &frequency,
                                    uint32_t timeout = DEFAULT_TIMEOUT);

  /**
   * @brief Increase the scanning frequency by 1.0 HZ \n
   * @param[in] frequency    scanning frequency
   * @param[in] timeout      timeout
   * @return return status
   * @retval RESULT_OK       success
   * @retval RESULT_FAILE    failed
   * @note Non-scan state, perform currect operation.
   */
  virtual result_t setScanFrequencyAdd(scan_frequency &frequency,
                                       uint32_t timeout = DEFAULT_TIMEOUT);

  /**
   * @brief Reduce the scanning frequency by 1.0 HZ \n
   * @param[in] frequency    scanning frequency
   * @param[in] timeout      timeout
   * @return return status
   * @retval RESULT_OK       success
   * @retval RESULT_FAILE    failed
   * @note Non-scan state, perform currect operation.
   */
  virtual result_t setScanFrequencyDis(scan_frequency &frequency,
                                       uint32_t timeout = DEFAULT_TIMEOUT);

  /**
   * @brief Increase the scanning frequency by 0.1 HZ \n
   * @param[in] frequency    scanning frequency
   * @param[in] timeout      timeout
   * @return return status
   * @retval RESULT_OK       success
   * @retval RESULT_FAILE    failed
   * @note Non-scan state, perform currect operation.
   */
  virtual result_t setScanFrequencyAddMic(scan_frequency &frequency,
                                          uint32_t timeout = DEFAULT_TIMEOUT);

  /**
   * @brief Reduce the scanning frequency by 0.1 HZ \n
   * @param[in] frequency    scanning frequency
   * @param[in] timeout      timeout
   * @return return status
   * @retval RESULT_OK       success
   * @retval RESULT_FAILE    failed
   * @note Non-scan state, perform currect operation.
   */
  virtual result_t setScanFrequencyDisMic(scan_frequency &frequency,
                                          uint32_t timeout = DEFAULT_TIMEOUT);

  /**
   * @brief Get lidar sampling frequency \n
   * @param[in] frequency    sampling frequency
   * @param[in] timeout      timeout
   * @return return status
   * @retval RESULT_OK       success
   * @retval RESULT_FAILE    failed
   * @note Non-scan state, perform currect operation.
   */
  virtual result_t getSamplingRate(sampling_rate &rate,
                                   uint32_t timeout = DEFAULT_TIMEOUT);

  /**
   * @brief Set the lidar sampling frequency \n
   * @param[in] rate    　　　sampling frequency
   * @param[in] timeout      timeout
   * @return return status
   * @retval RESULT_OK       success
   * @retval RESULT_FAILE    failed
   * @note Non-scan state, perform currect operation.
   */
  virtual result_t setSamplingRate(sampling_rate &rate,
                                   uint32_t timeout = DEFAULT_TIMEOUT);
  /**
   * @brief get lidar zero offset angle \n
   * @param[in] angle　　　   zero offset angle
   * @param[in] timeout      timeout
   * @return return status
   * @retval RESULT_OK       success
   * @retval RESULT_FAILE    failed
   * @note Non-scan state, perform currect operation.
   */
  virtual result_t getZeroOffsetAngle(offset_angle &angle,
                                      uint32_t timeout = DEFAULT_TIMEOUT);

  /**
  * @brief Get current scan configuration.
  * @returns scanCfg structure.
  */
  bool getScanCfg(lidarConfig &config, const std::string &ip_address = "");

  /**
  * @brief Get current scan update configuration.
  * @returns scanCfg structure.
  */
  lidarConfig getFinishedScanCfg();

  /**
   * @brief updateScanCfg
   * @param config
   */
  void updateScanCfg(const lidarConfig &config);
```

## Parameter Table

The Table that the user uses to perform parameter related operations:

- Set the parameter related API by table.

For additional information and examples, refer to [Parameter](#code-example)

### Table List - Models
|LIDAR | Model  |  Baudrate |  SampleRate(K) | Range(m)  		 |  Frequency(HZ) | Intenstiy(bit) | SingleChannel | voltage(V)|
| :--- |:--:|:--:|:--:|:--:|:--:|:--:|:--:|:--:|
| F4 | 1	 |  115200 | 4 |  0.12~12 | 5~12 | false | false 	  | 4.8~5.2 |
| S4 | 4	 |  115200 | 4 |  0.10~8.0 | 5~12 (PWM) | false | false 	  | 4.8~5.2 |
| S4B | 4/11 |  153600 | 4 |  0.10~8.0 | 5~12(PWM) | true(8) | false 	  | 4.8~5.2 |
| S2 | 4/12 |  115200 | 3 |  0.10~8.0 	| 4~8(PWM) | false | true 		  | 4.8~5.2 |
| G4 | 5	 |  230400 | 9/8/4 |  0.28/0.26/0.1~16| 5~12 	  | false | false 	  | 4.8~5.2 |
| X4 | 6	 |  128000 | 5 |  0.12~10 		| 5~12(PWM) | false | false 	  | 4.8~5.2 |
| X2/X2L | 6	 |  115200 | 3 |  0.10~8.0 	| 4~8(PWM) | false | true 		  | 4.8~5.2 |
| G4PRO | 7	 |  230400 | 9/8/4 |  0.28/0.26/0.1~16| 5~12 	  | false | false 	  | 4.8~5.2 |
| F4PRO | 8	 |  230400 | 4/6 |  0.12~12 | 5~12 	  | false | false 	  | 4.8~5.2 |
| R2 | 9	 |  230400 | 5 |  0.12~16 		| 5~12 	  | false | false 	  | 4.8~5.2 |
| G6 | 13 |  512000 | 18/16/8 |  0.28/0.26/0.1~25| 5~12 	  | false | false 	  | 4.8~5.2 |
| G2A | 14	 |  230400 | 5 |  0.12~12 | 5~12 	  | false | false 	  | 4.8~5.2 |
| G2 | 15		|  230400 | 5 |  0.28~16 		| 5~12 	  | true(8) | false 	  | 4.8~5.2 |
| G2C | 16		|  115200 | 4 |  0.1~12 	| 5~12 	  | false 	 | false 	  | 4.8~5.2 |
| G4B | 17		|  512000 | 10 |  0.12~16 | 5~12 	  | true(10) | false 	  | 4.8~5.2 |
| G4C | 18		|  115200 | 4 |  0.1~12		 | 5~12 | false | false 	  | 4.8~5.2 |
| G1 | 19		|  230400 | 9 |  0.28~16 | 5~12 	  | false | false 	  | 4.8~5.2 |
| TX8 　 | 100	 |  115200 | 4 |  0.1~8 	 | 4~8(PWM) | false | true 	  | 4.8~5.2 |
| TX20 　| 100	 |  115200 | 4 |  0.1~20 	 | 4~8(PWM) | false | true 	  | 4.8~5.2 |
| TG15 　| 100	 |  512000 | 20/18/10 |  0.05~30 	| 3~16 	  | false | false 	  | 4.8~5.2 |
| TG30 　| 101	 |  512000 | 20/18/10 |  0.05~30 	| 3~16 	  | false | false 	  | 4.8~5.2 |
| TG50 　| 102	 |  512000 | 20/18/10 |  0.05~50 	| 3~16 	  | false | false 	  | 4.8~5.2 |
| T15 　 | 200	 |  8000 | 20 |  0.05~15 	| 10-35 	  | true | false 	  | 4.8~5.2 |
| T30 　 | 200	 |  8000 | 20 |  0.05~30 	| 10-35 	  | true | false 	  | 4.8~5.2 |

### Table List - SerialBaudrate
  <table>
       <tr><th>LiDAR                               <th>SerialBaudrate
       <tr><th>F4/S2/X2/X2L/S4/TX8/TX20/G4C        <td>115200
       <tr><th>X4                                  <td>128000
       <tr><th>S4B                                 <td>153600
       <tr><th>G1/G2/R2/G4/G4PRO/F4PRO             <td>230400
       <tr><th>G2A/G2C                             <td>230400
       <tr><th>G6/G4B/TG15/TG30/TG50               <td>512000
       <tr><th>T5/T15(network)                     <td>8000
   </table>

### Table List - SampleRate
   <table>
        <tr><th>LiDAR               <td>SampleRate
        <tr><th>G4/F4               <td>4,8,9
        <tr><th>F4PRO               <td>4,6
        <tr><th>G6                  <td>8,16,18
        <tr><th>G4B                 <td>10
        <tr><th>G1                  <td>9
        <tr><th>G2A/G2/R2/X4        <td>5
        <tr><th>S4/S4B/G4C/TX8/TX20 <td>4
        <tr><th>G2C                 <td>4
        <tr><th>S2                  <td>3
        <tr><th>TG15/TG30/TG50      <td>10,18,20
        <tr><th>T5/T15              <td>20
    </table>

### Table List - ScanFrequency
<table>
        <tr><th>LiDAR                           <td>ScanFrequency
        <tr><th>S2/X2/X2L/TX8/TX20              <td>4~8(PWM)
        <tr><th>F4/F4PRO/G4/G4PRO/R2            <td>5~12
        <tr><th>G6/G2A/G2/G2C/G4B/G4C/G1        <td>5~12
        <tr><th>S4/S4B/X4                       <td>5~12(PWM)
        <tr><th>TG15/TG30/TG50                  <td>3~16
        <tr><th>T5/T15                          <td>5~40
    </table>

### Table List - SingleChannel
<table>
        <tr><th>LiDAR                                 <th> SingleChannel
        <tr><th>G1/G2/G2A/G2C                          <td>false
        <tr><th>G4/G4B/G4PRO/G6/F4/F4PRO               <td>false
        <tr><th>S4/S4B/X4/R2/G4C                       <td>false
        <tr><th>S2/X2/X2L                              <td>true
        <tr><th>TG15/TG30/TG50                         <td>false
        <tr><th>TX8/TX20                               <td>true
        <tr><th>T5/T15                                 <td>false
        <tr><th>                                       <td>true
</table>

### Table List - LidarType
  <table>
       <tr><th>LiDAR                            <th> LidarType
       <tr><th>G1/G2A/G2/G2C                    <td>TYPE_TRIANGLE
       <tr><th>G4/G4B/G4C/G4PRO                 <td>TYPE_TRIANGLE
       <tr><th>G6/F4/F4PRO                      <td>TYPE_TRIANGLE
       <tr><th>S4/S4B/X4/R2/S2/X2/X2L           <td>TYPE_TRIANGLE
       <tr><th>TG15/TG30/TG50/TX8/TX20          <td>TYPE_TOF
       <tr><th>T5/T15                           <td>TYPE_TOF_NET
   </table>

### Table List - Intensity
   <table>
        <tr><th>LiDAR                                  <th> Intensity
        <tr><th>S4B/G2/G4B                             <td>true
        <tr><th>G4/G4C/G4PRO/F4/F4PRO/G6               <td>false
        <tr><th>G1/G2A/G2C/R2                          <td>false
        <tr><th>S2/X2/X2L/X4                           <td>false
        <tr><th>TG15/TG30/TG50                         <td>false
        <tr><th>TX8/TX20                               <td>false
        <tr><th>T5/T15                                 <td>true
        <tr><th>                                       <td>false
    </table>

### Table List - SupportMotorDtrCtrl
   <table>
        <tr><th>S4/S4B/S2/X2/X2L/X4                    <th>SupportMotorDtrCtrl
        <tr><th>S4/S4B/S2/X2/X2L/X4                    <td>true
        <tr><th>TX8/TX20                               <td>true
        <tr><th>G4/G4C/G4PRO/F4/F4PRO/G6               <td>false
        <tr><th>G1/G2A/G2C/R2/G2/G4B                   <td>false
        <tr><th>TG15/TG30/TG50                         <td>false
        <tr><th>T5/T15                                 <td>false
    </table>

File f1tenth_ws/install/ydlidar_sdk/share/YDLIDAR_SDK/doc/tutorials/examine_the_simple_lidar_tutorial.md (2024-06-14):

# Examining the Simple Lidar Tutorial
Description: This tutorial examines running the simple lidar tutorial.
Tutorial Level: BEGINNER
Previous Tutorial: Writing a Simple Lidar Tutorial ([c](writing_lidar_tutorial_c.md))([python](writing_lidar_tutorial_python.md)) ([c++](writing_lidar_tutorial_c++.md))

## Table of Contents
- [Running the Lidar Turorial](#running-the-lidar-turorial)

### Running the Lidar Turorial
In the last tutorial we made a tutorial called "lidar_tutorial". Let's run it: 
```shell
./lidar_tutorial                (C++)(C)
python lidar_tutorial.py        (Python)
```
You will see something similar to: 

        YDLidar SDK initializing
        YDLidar SDK has been initialized
        [YDLIDAR]:SDK Version: 1.0.0
        LiDAR successfully connected
        [YDLIDAR]:Lidar running correctly ! The health status: good
        [YDLIDAR] Connection established in [/dev/ttyUSB0][230400]:
        Firmware version: 1.3
        Hardware version: 1
        Model: G4
        Serial: 2020010200010001
        [YDLIDAR INFO] Current Scan Frequency: 10.000000Hz
        LiDAR init success!
        [YDLIDAR]:Fixed Size: 900
        [YDLIDAR]:Sample Rate: 9K
        [YDLIDAR INFO] Current Sampling Rate : 9K
        [YDLIDAR INFO] Now YDLIDAR is scanning ......
        Scan received[1582955714469712000]: 964 ranges is [9.342144]Hz
        Scan received[1582955714607423000]: 954 ranges is [9.429421]Hz
        Scan received[1582955714742073000]: 949 ranges is [9.485030]Hz
        Scan received[1582955714875723000]: 946 ranges is [9.513148]Hz
        Scan received[1582955715008873000]: 943 ranges is [9.547170]Hz
        Scan received[1582955715141423000]: 938 ranges is [9.593015]Hz
        Scan received[1582955715273253000]: 933 ranges is [9.651109]Hz
        Scan received[1582955715404003000]: 930 ranges is [9.686395]Hz
        Scan received[1582955715534183000]: 928 ranges is [9.698230]Hz
        Scan received[1582955715664261000]: 919 ranges is [9.794232]Hz
        Scan received[1582955715792611000]: 906 ranges is [9.936508]Hz

When you are done, press Ctrl-C to terminate both the lidar tutorial. 

Note: ERROR
* ./lidar_tutorial: error while loading shared libraries: libydlidar_sdk.so: cannot open shared object file: No such file or directory
if the above error occurs, the  operation is as follows:

```shell
cat /etc/ld.so.conf
        include ld.so.conf.d/*.conf
## ydlidar_sdk library path added to ld.so.conf.
echo "/usr/local/lib" >> /etc/ld.so.conf
sudo ldconfig
```
OR
```shell
## ydlidar_sdk library path added to LD_LIBRARY_PATH
export LD_LIBRARY_PATH=/usr/local/lib:$LD_LIBRARY_PATH   
```

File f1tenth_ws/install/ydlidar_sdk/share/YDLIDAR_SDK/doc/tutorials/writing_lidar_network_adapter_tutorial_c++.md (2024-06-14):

# WritingLidarNetworkAdapterTutorial(c++)
Description: This tutorial covers how to write a lidar network adapter tutorial in C++.
Tutorial Level: BEGINNER
Next Tutorial: [Examining the simple lidar tutorial](examine_the_simple_lidar_tutorial.md)

## Table of Contents

- [Writing a Simple lidar tutorial (C++)](#writing-a-simple-lidar-tutorial-(C++))
    - [create beginner_tutorials directories](#create-beginner_tutorials-directories)
    - [The Code Explained](#the-code-explained)
- [Building your project](#building-your-project)

## Writing a Simple lidar tutorial (C++)
Description: This tutorial covers how to write a LiDAR network adapter data console program in C++.
Tutorial Level: BEGINNER

### create beginner_tutorials directories
```shell
mkdir beginner_tutorials
cd beginner_tutorials
```
### Create the lidar_tutorial.cpp file within the beginner_tutorials project and paste the following inside it: 
[https://github.com/YDLIDAR/ydlidar_tutorials/blob/master/cpp_tutorials/lidar_tutorial/lidar_tutorial.cpp](https://github.com/YDLIDAR/ydlidar_tutorials/blob/master/cpp_tutorials/lidar_tutorial/lidar_tutorial.cpp)

```c++
#include "CYdLidar.h"
#include <string>
using namespace std;
using namespace ydlidar;

#if defined(_MSC_VER)
#pragma comment(lib, "ydlidar_sdk.lib")
#endif

int main(int argc, char *argv[]) {
  // init system signal
  ydlidar::os_init();

  CYdLidar laser;
  //////////////////////string property/////////////////
  /// Lidar ports
  std::string port = "192.168.31.200;
  /// lidar port
  laser.setlidaropt(LidarPropSerialPort, port.c_str(), port.size());
  /// ignore array
  std::string ignore_array;
  ignore_array.clear();
  laser.setlidaropt(LidarPropIgnoreArray, ignore_array.c_str(),
                    ignore_array.size());

  //////////////////////int property/////////////////
  /// lidar port
  int optval = 8000;
  laser.setlidaropt(LidarPropSerialBaudrate, &optval, sizeof(int));
  /// tof lidar
  optval = TYPE_TRIANGLE;
  laser.setlidaropt(LidarPropLidarType, &optval, sizeof(int));
  /// device type
  optval = YDLIDAR_TYPE_TCP;
  laser.setlidaropt(LidarPropDeviceType, &optval, sizeof(int));
  /// sample rate
  optval = 9;
  laser.setlidaropt(LidarPropSampleRate, &optval, sizeof(int));
  /// abnormal count
  optval = 4;
  laser.setlidaropt(LidarPropAbnormalCheckCount, &optval, sizeof(int));

  //////////////////////bool property/////////////////
  /// fixed angle resolution
  bool b_optvalue = false;
  laser.setlidaropt(LidarPropFixedResolution, &b_optvalue, sizeof(bool));
  /// rotate 180
  laser.setlidaropt(LidarPropReversion, &b_optvalue, sizeof(bool));
  /// Counterclockwise
  laser.setlidaropt(LidarPropInverted, &b_optvalue, sizeof(bool));
  b_optvalue = true;
  laser.setlidaropt(LidarPropAutoReconnect, &b_optvalue, sizeof(bool));
  /// one-way communication
  b_optvalue = false;
  laser.setlidaropt(LidarPropSingleChannel, &b_optvalue, sizeof(bool));
  /// intensity
  b_optvalue = false;
  laser.setlidaropt(LidarPropIntenstiy, &b_optvalue, sizeof(bool));
  /// Motor DTR
  b_optvalue = false;
  laser.setlidaropt(LidarPropSupportMotorDtrCtrl, &b_optvalue, sizeof(bool));

  //////////////////////float property/////////////////
  /// unit: °
  float f_optvalue = 180.0f;
  laser.setlidaropt(LidarPropMaxAngle, &f_optvalue, sizeof(float));
  f_optvalue = -180.0f;
  laser.setlidaropt(LidarPropMinAngle, &f_optvalue, sizeof(float));
  /// unit: m
  f_optvalue = 16.f;
  laser.setlidaropt(LidarPropMaxRange, &f_optvalue, sizeof(float));
  f_optvalue = 0.1f;
  laser.setlidaropt(LidarPropMinRange, &f_optvalue, sizeof(float));
  /// unit: Hz
  f_optvalue = 10.f;
  laser.setlidaropt(LidarPropScanFrequency, &f_optvalue, sizeof(float));

  // initialize SDK and LiDAR
  bool ret = laser.initialize();
  if (ret) {//success
    //Start the device scanning routine which runs on a separate thread and enable motor.
    ret = laser.turnOn();
  } else {
    fprintf(stderr, "%s\n", laser.DescribeError());
    fflush(stderr);
  }

  // Turn On success and loop  
  while (ret && ydlidar::os_isOk()) {
    LaserScan scan;
    if (laser.doProcessSimple(scan)) {
      fprintf(stdout, "Scan received[%llu]: %u ranges is [%f]Hz\n",
              scan.stamp,
              (unsigned int)scan.points.size(), 1.0 / scan.config.scan_time);
      fflush(stdout);
    } else {
      fprintf(stderr, "Failed to get Lidar Data\n");
      fflush(stderr);
    }
  }
  // Stop the device scanning thread and disable motor.
  laser.turnOff();
  // Uninitialize the SDK and Disconnect the LiDAR.
  laser.disconnecting();
  return 0;
}
```

Note: The difference form the serial port is the following three properties
* LidarPropSerialPort
* LidarPropSerialBaudrate
* LidarPropDeviceType
When the network adapter board is connected to the lidar, `LidarPropSerialPort` is the lidar IP address and `LidarPropSerialBaudrate` is the lidar network port.
The device type `LidarPropDeviceType` value is changed from the `YDLIDAR_TYPE_SERIAL` to `YDLIDAR_TYPE_TCP`.

### The Code Explained
Now, let's break the code down. 
```c++
#include "CYdLidar.h"
```
CYdLidar.h is a convenience include that includes all the headers necessary to use the most common public pieces of the YDLIDAR SDK. 

```c++
  ydlidar::os_init();
```
Initialize system signal. install a SIGINT handler which provides Ctrl-C handling

```c++
  CYdLidar laser;
```
Create a handle to this Lidar. 

```c++
 //////////////////////string property/////////////////
  /// Lidar ports
  std::string port = "192.168.31.200";
```
Query avaliable Lidar IP .

```c++
  /// lidar port
  laser.setlidaropt(LidarPropSerialPort, port.c_str(), port.size());
  /// ignore array
  std::string ignore_array;
  ignore_array.clear();
  laser.setlidaropt(LidarPropIgnoreArray, ignore_array.c_str(),
                    ignore_array.size());
```
Set Lidar string property paramters.

```c++
  //////////////////////int property/////////////////
  /// lidar port
  int optval = 8000;
  laser.setlidaropt(LidarPropSerialBaudrate, &optval, sizeof(int));
  /// tof lidar
  optval = TYPE_TRIANGLE;
  laser.setlidaropt(LidarPropLidarType, &optval, sizeof(int));
  /// device type
  optval = YDLIDAR_TYPE_TCP;
  laser.setlidaropt(LidarPropDeviceType, &optval, sizeof(int));
  /// sample rate
  optval = 9;
  laser.setlidaropt(LidarPropSampleRate, &optval, sizeof(int));
  /// abnormal count
  optval = 4;
  laser.setlidaropt(LidarPropAbnormalCheckCount, &optval, sizeof(int));

```
Set Lidar string int paramters.

```c++
  //////////////////////bool property/////////////////
  /// fixed angle resolution
  bool b_optvalue = false;
  laser.setlidaropt(LidarPropFixedResolution, &b_optvalue, sizeof(bool));
  /// rotate 180
  laser.setlidaropt(LidarPropReversion, &b_optvalue, sizeof(bool));
  /// Counterclockwise
  laser.setlidaropt(LidarPropInverted, &b_optvalue, sizeof(bool));
  b_optvalue = true;
  laser.setlidaropt(LidarPropAutoReconnect, &b_optvalue, sizeof(bool));
  /// one-way communication
  b_optvalue = false;
  laser.setlidaropt(LidarPropSingleChannel, &b_optvalue, sizeof(bool));
  /// intensity
  b_optvalue = false;
  laser.setlidaropt(LidarPropIntenstiy, &b_optvalue, sizeof(bool));
  /// Motor DTR
  b_optvalue = false;
  laser.setlidaropt(LidarPropSupportMotorDtrCtrl, &b_optvalue, sizeof(bool));

```
Set Lidar bool property paramters.

```c++
  //////////////////////float property/////////////////
  /// unit: °
  float f_optvalue = 180.0f;
  laser.setlidaropt(LidarPropMaxAngle, &f_optvalue, sizeof(float));
  f_optvalue = -180.0f;
  laser.setlidaropt(LidarPropMinAngle, &f_optvalue, sizeof(float));
  /// unit: m
  f_optvalue = 16.f;
  laser.setlidaropt(LidarPropMaxRange, &f_optvalue, sizeof(float));
  f_optvalue = 0.1f;
  laser.setlidaropt(LidarPropMinRange, &f_optvalue, sizeof(float));
  /// unit: Hz
  f_optvalue = 10.f;
  laser.setlidaropt(LidarPropScanFrequency, &f_optvalue, sizeof(float));
```
Set Lidar float property paramters.

```c++
  // initialize SDK and LiDAR
  bool ret = laser.initialize();
```
Initialize the SDK and LiDAR.

`initialize` will return false if:
+ Serial port does not correspond to the actual Lidar.
+ Serial port does not have read and write permissions.
+ Lidar baud rate settings error.
+ Incorrect Lidar type setting.

```c++
  if (ret) {//success
    //Start the device scanning routine which runs on a separate thread and enable motor.
    ret = laser.turnOn();
  } else {
    fprintf(stderr, "%s\n", laser.DescribeError());
    fflush(stderr);
  }
```
Start the device scanning routine which runs on a separate thread and enable motor.

`turnOn` will return false if:
+ Lidar stall.
+ Lidar power suppy is unstable.

```c++
  // Turn On success and loop  
  while (ret && ydlidar::os_isOk()) {
```
By `ydlidar::os_init()` will install a SIGINT handler which provides Ctrl-C handling which will cause `ydlidar::os_isOk()` to return false if that happens.

`ydlidar::os_isOk()` will return false if:
+ a SIGINT is received (Ctrl-C)
+ ydlidar::os_shutdown() has been called by another part of the application.

Once `ydlidar::os_isOk()` returns false, Loop exit.

```c++
    LaserScan scan;
    if (laser.doProcessSimple(scan)) {
      fprintf(stdout, "Scan received[%llu]: %u ranges is [%f]Hz\n",
              scan.stamp,
              (unsigned int)scan.points.size(), 1.0 / scan.config.scan_time);
      fflush(stdout);
    } else {
      fprintf(stderr, "Failed to get Lidar Data\n");
      fflush(stderr);
    }
```
Get the LiDAR Scan Data.

```c++
  // Stop the device scanning thread and disable motor.
  laser.turnOff();
```
Stop the device scanning thread and disable motor.

```c++
  // Uninitialize the SDK and Disconnect the LiDAR.
  laser.disconnecting();
```
Uninitialize the SDK and Disconnect the LiDAR.

## Building your project
You need to create a CMakeLists.txt file.

The generated CMakeLists.txt should look like this:
[https://github.com/YDLIDAR/ydlidar_tutorials/blob/master/cpp_tutorials/lidar_tutorial/CMakeLists.txt](https://github.com/YDLIDAR/ydlidar_tutorials/blob/master/cpp_tutorials/lidar_tutorial/CMakeLists.txt)

```cmake
cmake_minimum_required(VERSION 2.8)
PROJECT(lidar_tutorial)
set(CMAKE_CXX_FLAGS "${CMAKE_CXX_FLAGS} -std=c++11")
add_definitions(-std=c++11) # Use C++11

#Include directories
include_directories(
     ${CMAKE_SOURCE_DIR}
)
############## YDLIDAR SDK START#####################################
#find ydlidar_sdk package
find_package(ydlidar_sdk REQUIRED)
#Include directories
include_directories(
  ${YDLIDAR_SDK_INCLUDE_DIRS}
)

#link library directories
link_directories(${YDLIDAR_SDK_LIBRARY_DIRS})

add_executable(${PROJECT_NAME} lidar_tutorial.cpp)

#Link your project to ydlidar_sdk library.
target_link_libraries(${PROJECT_NAME} ${YDLIDAR_SDK_LIBRARIES})

############## YDLIDAR SDK END#####################################
```
This will create one executable, lidar_tutorial, which by default will go into package directory of your build space.

Linux:
  * `YDLIDAR_SDK_LIBRARIES` includes `ydlidar_sdk pthread rt`
  * If you need the pthread library at the end of the compilation flag,
   you need to put `YDLIDAR_SDK_LIBRARIES` at the end.

you can use the following variable to depend on all necessary targets: 

```cmake
target_link_libraries(${PROJECT_NAME} ${YDLIDAR_SDK_LIBRARIES})
```
Now run cmake: 
```cmake
# In your project directory
mkdir build
cd build
cmake ..
make j4  
```
Now that you have written a simple lidar tutorial, let's [examine the simple lidar tutorial](examine_the_simple_lidar_tutorial.md).

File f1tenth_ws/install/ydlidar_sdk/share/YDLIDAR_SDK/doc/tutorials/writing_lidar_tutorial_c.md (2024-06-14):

# WritingLidarTutorial(C)
Description: This tutorial covers how to write a lidar tutorial in C.
Tutorial Level: BEGINNER
Next Tutorial: [Examining the simple lidar tutorial](examine_the_simple_lidar_tutorial.md)

## Table of Contents

- [Writing a Simple lidar tutorial (C)](#writing-a-simple-lidar-tutorial-(C))
    - [create beginner_tutorials directories](#create-beginner_tutorials-directories)
    - [The Code Explained](#the-code-explained)
- [Building your project](#building-your-project)

## Writing a Simple lidar tutorial (C)
Description: This tutorial covers how to write a LiDAR data console program in C.
Tutorial Level: BEGINNER

### create beginner_tutorials directories
```shell
mkdir beginner_tutorials
cd beginner_tutorials
```
### Create the lidar_tutorial.cpp file within the beginner_tutorials project and paste the following inside it: 
[https://github.com/YDLIDAR/ydlidar_tutorials/blob/master/c_tutorials/lidar_tutorial/lidar_tutorial.c](https://github.com/YDLIDAR/ydlidar_tutorials/blob/master/c_tutorials/lidar_tutorial/lidar_tutorial.c)

```c
//
// The MIT License (MIT)
//
// Copyright (c) 2019 EAIBOT. All rights reserved.
//
// Permission is hereby granted, free of charge, to any person obtaining a copy
// of this software and associated documentation files (the "Software"), to deal
// in the Software without restriction, including without limitation the rights
// to use, copy, modify, merge, publish, distribute, sublicense, and/or sell
// copies of the Software, and to permit persons to whom the Software is
// furnished to do so, subject to the following conditions:
//
// The above copyright notice and this permission notice shall be included in
// all copies or substantial portions of the Software.
//
// THE SOFTWARE IS PROVIDED "AS IS", WITHOUT WARRANTY OF ANY KIND, EXPRESS OR
// IMPLIED, INCLUDING BUT NOT LIMITED TO THE WARRANTIES OF MERCHANTABILITY,
// FITNESS FOR A PARTICULAR PURPOSE AND NONINFRINGEMENT. IN NO EVENT SHALL THE
// AUTHORS OR COPYRIGHT HOLDERS BE LIABLE FOR ANY CLAIM, DAMAGES OR OTHER
// LIABILITY, WHETHER IN AN ACTION OF CONTRACT, TORT OR OTHERWISE, ARISING FROM,
// OUT OF OR IN CONNECTION WITH THE SOFTWARE OR THE USE OR OTHER DEALINGS IN THE
// SOFTWARE.
//

#include <stdio.h>
#include <stdlib.h>
#include <string.h>
#ifdef WIN32
#include <windows.h>
#else
#include <unistd.h>
#endif
#include "ydlidar_sdk.h"

#if defined(_MSC_VER)
#pragma comment(lib, "ydlidar_sdk.lib")
#endif

int main(int argc, const char *argv[]) {

    os_init();
    YDLidar *laser = lidarCreate();
    //string prop
    char port[50] = "/dev/ydlidar";
    LidarPort ports;
    int size = lidarPortList(&ports);
    int i = 0;
    for(i =0; i < size; i++) {
        printf("port: %s\n", ports.port[i].data);
        /// last port
        strcpy(port, ports.port[i].data);
    }
    setlidaropt(laser, LidarPropSerialPort, port, sizeof(port));
    strcpy(port, "");
    setlidaropt(laser, LidarPropIgnoreArray,port, sizeof(port));

    //int prop
    int i_optvalue = 512000;
    setlidaropt(laser, LidarPropSerialBaudrate, &i_optvalue, sizeof(int));
    i_optvalue = TYPE_TOF;
    setlidaropt(laser, LidarPropLidarType, &i_optvalue, sizeof(int));
    i_optvalue = YDLIDAR_TYPE_SERIAL;
    setlidaropt(laser, LidarPropDeviceType, &i_optvalue, sizeof(int));
    i_optvalue = 20;
    setlidaropt(laser, LidarPropSampleRate, &i_optvalue, sizeof(int));

    //bool prop
    bool b_optval = true;
    setlidaropt(laser, LidarPropAutoReconnect, &b_optval, sizeof(bool));
    b_optval = false;
    setlidaropt(laser, LidarPropSingleChannel, &b_optval, sizeof(bool));
    setlidaropt(laser, LidarPropIntenstiy, &b_optval, sizeof(bool));
    setlidaropt(laser, LidarPropInverted, &b_optval, sizeof(bool));
    setlidaropt(laser, LidarPropReversion, &b_optval, sizeof(bool));
    setlidaropt(laser, LidarPropSupportMotorDtrCtrl, &b_optval, sizeof(bool));
    setlidaropt(laser, LidarPropFixedResolution, &b_optval, sizeof(bool));

    //float prop
    float f_optval = 10.f;
    setlidaropt(laser, LidarPropScanFrequency, &f_optval, sizeof(float));
    f_optval = 180.0f;
    setlidaropt(laser, LidarPropMaxAngle, &f_optval, sizeof(float));
    f_optval = -180.0f;
    setlidaropt(laser, LidarPropMinAngle, &f_optval, sizeof(float));
    f_optval = 64.f;
    setlidaropt(laser, LidarPropMaxRange, &f_optval, sizeof(float));
    f_optval = 0.05f;
    setlidaropt(laser, LidarPropMinRange, &f_optval, sizeof(float));

    getlidaropt(laser, LidarPropSerialBaudrate,&i_optvalue, sizeof(int));
    printf("baudrate: %d\n", i_optvalue);

    bool ret = initialize(laser);
    if(ret) {
        ret = turnOn(laser);
    }

    LaserFan scan;
    LaserFanInit(&scan);
    while (ret && os_isOk()) {
        if(doProcessSimple(laser, &scan)) {
            fprintf(stdout, "Scan received[%llu]: %u ranges is [%f]Hz\n",
                    scan.stamp,
                    (unsigned int)scan.npoints, 1.0 / scan.config.scan_time);
            fflush(stdout);
        } else {
            fprintf(stderr, "Failed to get Lidar Data\n");
            fflush(stderr);
        }
    }
    LaserFanDestroy(&scan);
    turnOff(laser);
    disconnecting(laser);
    lidarDestroy(&laser);
    return 0;

}
```

### The Code Explained
Now, let's break the code down. 
```c++
#include "ydlidar_sdk.h"
```
ydlidar_sdk.h is a convenience include that includes all the headers necessary to use the most common public pieces of the YDLIDAR SDK. 

```c
  os_init();
```
Initialize system signal. install a SIGINT handler which provides Ctrl-C handling

```c
  YDLidar *laser = lidarCreate();
```
Create a handle to this Lidar. 

```c
  //string prop
  char port[50] = "/dev/ydlidar";
  LidarPort ports;
  int size = lidarPortList(&ports);
  int i = 0;
  for(i =0; i < size; i++) {
      printf("port: %s\n", ports.port[i].data);
      /// last port
      strcpy(port, ports.port[i].data);
  }
```
Query avaliable Lidar ports.

```c
  setlidaropt(laser, LidarPropSerialPort, port, sizeof(port));
  strcpy(port, "");
  setlidaropt(laser, LidarPropIgnoreArray,port, sizeof(port));
```
Set Lidar string property paramters.

```c
  //int prop
  int i_optvalue = 512000;
  setlidaropt(laser, LidarPropSerialBaudrate, &i_optvalue, sizeof(int));
  i_optvalue = TYPE_TOF;
  setlidaropt(laser, LidarPropLidarType, &i_optvalue, sizeof(int));
  i_optvalue = YDLIDAR_TYPE_SERIAL;
  setlidaropt(laser, LidarPropDeviceType, &i_optvalue, sizeof(int));
  i_optvalue = 20;
  setlidaropt(laser, LidarPropSampleRate, &i_optvalue, sizeof(int));
```
Set Lidar string int paramters.

```c
  //bool prop
  bool b_optval = true;
  setlidaropt(laser, LidarPropAutoReconnect, &b_optval, sizeof(bool));
  b_optval = false;
  setlidaropt(laser, LidarPropSingleChannel, &b_optval, sizeof(bool));
  setlidaropt(laser, LidarPropIntenstiy, &b_optval, sizeof(bool));
  setlidaropt(laser, LidarPropInverted, &b_optval, sizeof(bool));
  setlidaropt(laser, LidarPropReversion, &b_optval, sizeof(bool));
  setlidaropt(laser, LidarPropSupportMotorDtrCtrl, &b_optval, sizeof(bool));
  setlidaropt(laser, LidarPropFixedResolution, &b_optval, sizeof(bool));
```
Set Lidar bool property paramters.

```c
  //float prop
  float f_optval = 10.f;
  setlidaropt(laser, LidarPropScanFrequency, &f_optval, sizeof(float));
  f_optval = 180.0f;
  setlidaropt(laser, LidarPropMaxAngle, &f_optval, sizeof(float));
  f_optval = -180.0f;
  setlidaropt(laser, LidarPropMinAngle, &f_optval, sizeof(float));
  f_optval = 64.f;
  setlidaropt(laser, LidarPropMaxRange, &f_optval, sizeof(float));
  f_optval = 0.05f;
  setlidaropt(laser, LidarPropMinRange, &f_optval, sizeof(float));
```
Set Lidar float property paramters.

```c
  // initialize SDK and LiDAR
  bool ret = initialize(laser);
```
Initialize the SDK and LiDAR.

`initialize` will return false if:
+ Serial port does not correspond to the actual Lidar.
+ Serial port does not have read and write permissions.
+ Lidar baud rate settings error.
+ Incorrect Lidar type setting.

```c
  if(ret) {
    ret = turnOn(laser);
  }
```
Start the device scanning routine which runs on a separate thread and enable motor.

`turnOn` will return false if:
+ Lidar stall.
+ Lidar power suppy is unstable.

```c
  // Turn On success and loop  
  LaserFan scan;
  LaserFanInit(&scan);
  while (ret && os_isOk()) {
```
By `os_init()` will install a SIGINT handler which provides Ctrl-C handling which will cause `os_isOk()` to return false if that happens.

`os_isOk()` will return false if:
+ a SIGINT is received (Ctrl-C)
+ ydlidar::os_shutdown() has been called by another part of the application.

Once `os_isOk()` returns false, Loop exit.
Note: 
+ `LaserFan` need to be initialized with `LaserFanInit`
- After `LaserFan` leaves the Scope, it need to be destroyed with `LaserFanDestroy`, otherwisw it will leak memory.

```c
    if(doProcessSimple(laser, &scan)) {
        fprintf(stdout, "Scan received[%llu]: %u ranges is [%f]Hz\n",
                scan.stamp,
                (unsigned int)scan.npoints, 1.0 / scan.config.scan_time);
        fflush(stdout);
    } else {
        fprintf(stderr, "Failed to get Lidar Data\n");
        fflush(stderr);
    }
```
Get the LiDAR Scan Data.

```c
  LaserFanDestroy(&scan);
```
Destroy LaserFan, Free up memory.
Note:
  + After `LaserFan` leaves the Scope, it need to be destroyed with `LaserFanDestroy`, otherwisw it will leak memory.

```c
  // Stop the device scanning thread and disable motor.
  turnOff(laser);
```
Stop the device scanning thread and disable motor.

```c
  // Uninitialize the SDK and Disconnect the LiDAR.
  disconnecting(laser);
```
Uninitialize the SDK and Disconnect the LiDAR.

```
  lidarDestroy(&laser);
```
Destroy YDLidar, Free up memory.

## Building your project
You need to create a CMakeLists.txt file.

The generated CMakeLists.txt should look like this:
[https://github.com/YDLIDAR/ydlidar_tutorials/blob/master/c_tutorials/lidar_tutorial/CMakeLists.txt](https://github.com/YDLIDAR/ydlidar_tutorials/blob/master/c_tutorials/lidar_tutorial/CMakeLists.txt)

```cmake
cmake_minimum_required(VERSION 2.8)
PROJECT(lidar_tutorial C)

#Include directories
include_directories(
     ${CMAKE_SOURCE_DIR}
)
############## YDLIDAR SDK START#####################################
#find ydlidar_sdk package
find_package(ydlidar_sdk REQUIRED)
#Include directories
include_directories(
  ${YDLIDAR_SDK_INCLUDE_DIRS}
)
#link library directories
link_directories(${YDLIDAR_SDK_LIBRARY_DIRS})

add_executable(${PROJECT_NAME} lidar_tutorial.c)
#Link your project to ydlidar_sdk library.
target_link_libraries(${PROJECT_NAME} ${YDLIDAR_SDK_LIBRARIES} -lstdc++ -lm)

############## YDLIDAR SDK END#####################################
```
This will create one executable, lidar_tutorial, which by default will go into package directory of your build space.

ydlidar_sdk dependent libraries
  * C++ standard library.
  * math library.

Note:
* GCC CCLDFLAGS requires "-lstdc++ -lm".

you can use the following variable to depend on all necessary targets: 

```cmake
target_link_libraries(${PROJECT_NAME} ${YDLIDAR_SDK_LIBRARIES} -lstdc++ -lm)
```
Now run cmake: 
```cmake
# In your project directory
mkdir build
cd build
cmake ..
make j4  
```
Now that you have written a simple lidar tutorial, let's [examine the simple lidar tutorial](examine_the_simple_lidar_tutorial.md).

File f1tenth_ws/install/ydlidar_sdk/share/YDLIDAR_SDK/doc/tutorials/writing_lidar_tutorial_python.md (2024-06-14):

# WritingLidarTutorial(python)
Description: This tutorial covers how to write a lidar tutorial in Python.
Tutorial Level: BEGINNER
Next Tutorial: [Examining the simple lidar tutorial](examine_the_simple_lidar_tutorial.md)

## Table of Contents

- [Writing a Simple lidar tutorial (Python)](#writing-a-simple-lidar-tutorial-(python))
    - [create beginner_tutorials directories](#create-beginner_tutorials-directories)
    - [The Code Explained](#the-code-explained)
    
## Writing a Simple lidar tutorial (Python)
Description: This tutorial covers how to write a LiDAR data console program in Python.
Tutorial Level: BEGINNER

### create beginner_tutorials directories
```shell
mkdir beginner_tutorials
cd beginner_tutorials
```
### Create the lidar_tutorial.py file within the beginner_tutorials project and paste the following inside it: 
[https://github.com/YDLIDAR/ydlidar_tutorials/blob/master/pyhton_tutorials/lidar_tutorial/lidar_tutorial.py](https://github.com/YDLIDAR/ydlidar_tutorials/blob/master/python_tutorials/lidar_tutorial/lidar_tutorial.py)

```python
import os
import ydlidar

if __name__ == "__main__":
    ydlidar.os_init();
    laser = ydlidar.CYdLidar();
    ports = ydlidar.lidarPortList();
    port = "/dev/ydlidar";
    for key, value in ports.items():
        port = value;
    laser.setlidaropt(ydlidar.LidarPropSerialPort, port);
    laser.setlidaropt(ydlidar.LidarPropSerialBaudrate, 512000);
    laser.setlidaropt(ydlidar.LidarPropLidarType, ydlidar.TYPE_TOF);
    laser.setlidaropt(ydlidar.LidarPropDeviceType, ydlidar.YDLIDAR_TYPE_SERIAL);
    laser.setlidaropt(ydlidar.LidarPropScanFrequency, 10.0);
    laser.setlidaropt(ydlidar.LidarPropSampleRate, 20);
    laser.setlidaropt(ydlidar.LidarPropSingleChannel, False);

    ret = laser.initialize();
    if ret:
        ret = laser.turnOn();
        scan = ydlidar.LaserScan()
        while ret and ydlidar.os_isOk() :
            r = laser.doProcessSimple(scan);
            if r:
                print("Scan received[",scan.stamp,"]:",scan.points.size(),"ranges is [",1.0/scan.config.scan_time,"]Hz");
            else :
                print("Failed to get Lidar Data.")
        laser.turnOff();
    laser.disconnecting();
```

### The Code Explained
Now, let's break the code down. 
```python
import ydlidar
```
You need to import ydlidar if you are writing a YDLIDAR SDK.  

```python
  ydlidar.os_init();
```
Initialize system signal. install a SIGINT handler which provides Ctrl-C handling

```python
  laser = ydlidar.CYdLidar();
```
Create a handle to this Lidar. 

```python
    ports = ydlidar.lidarPortList();
    port = "/dev/ydlidar";
    for key, value in ports.items():
      port = value;
```
Query avaliable Lidar ports.

```python
    laser.setlidaropt(ydlidar.LidarPropSerialPort, port);
    laser.setlidaropt(ydlidar.LidarPropSerialBaudrate, 512000);
    laser.setlidaropt(ydlidar.LidarPropLidarType, ydlidar.TYPE_TOF);
    laser.setlidaropt(ydlidar.LidarPropDeviceType, ydlidar.YDLIDAR_TYPE_SERIAL);
    laser.setlidaropt(ydlidar.LidarPropScanFrequency, 10.0);
    laser.setlidaropt(ydlidar.LidarPropSampleRate, 20);
    laser.setlidaropt(ydlidar.LidarPropSingleChannel, False);
```
Set Lidar property paramters.

```c++
  // initialize SDK and LiDAR
  ret = laser.initialize();
```
Initialize the SDK and LiDAR.

`initialize` will return false if:
+ Serial port does not correspond to the actual Lidar.
+ Serial port does not have read and write permissions.
+ Lidar baud rate settings error.
+ Incorrect Lidar type setting.

```python 
      if ret:
        ret = laser.turnOn();
```
Start the device scanning routine which runs on a separate thread and enable motor.

`turnOn` will return false if:
+ Lidar stall.
+ Lidar power suppy is unstable.

```python
  // Turn On success and loop  
  while ret and ydlidar.os_isOk() :
```
By `ydlidar.os_isOk()` will install a SIGINT handler which provides Ctrl-C handling which will cause `ydlidar.os_isOk()` to return false if that happens.

`ydlidar.os_isOk()` will return false if:
+ a SIGINT is received (Ctrl-C)
+ ydlidar.os_shutdown() has been called by another part of the application.

Once `ydlidar.os_isOk()` returns false, Loop exit.

```pyhton
      r = laser.doProcessSimple(scan);
      if r:
        print("Scan received[",scan.stamp,"]:",scan.points.size(),"ranges is [",1.0/scan.config.scan_time,"]Hz");
      else :
        print("Failed to get Lidar Data.")
```
Get the LiDAR Scan Data.

```python
  // Stop the device scanning thread and disable motor.
  laser.turnOff();
```
Stop the device scanning thread and disable motor.

```pyhton
  // Uninitialize the SDK and Disconnect the LiDAR.
  laser.disconnecting();
```
Uninitialize the SDK and Disconnect the LiDAR.

Now that you have written a simple lidar tutorial, let's [examine the simple lidar tutorial](examine_the_simple_lidar_tutorial.md).

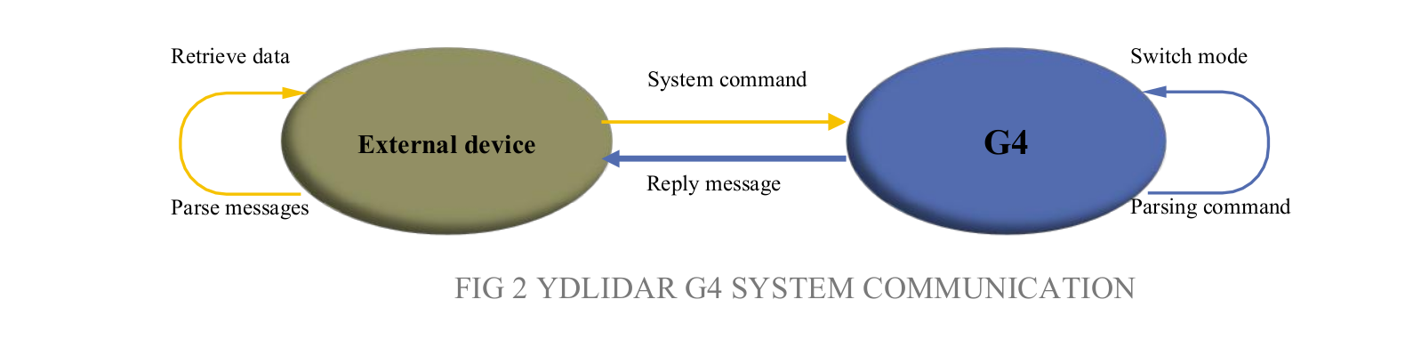
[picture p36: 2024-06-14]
f1tenth_ws/install/ydlidar_sdk/share/YDLIDAR_SDK/doc/images/communication_mechanism.png

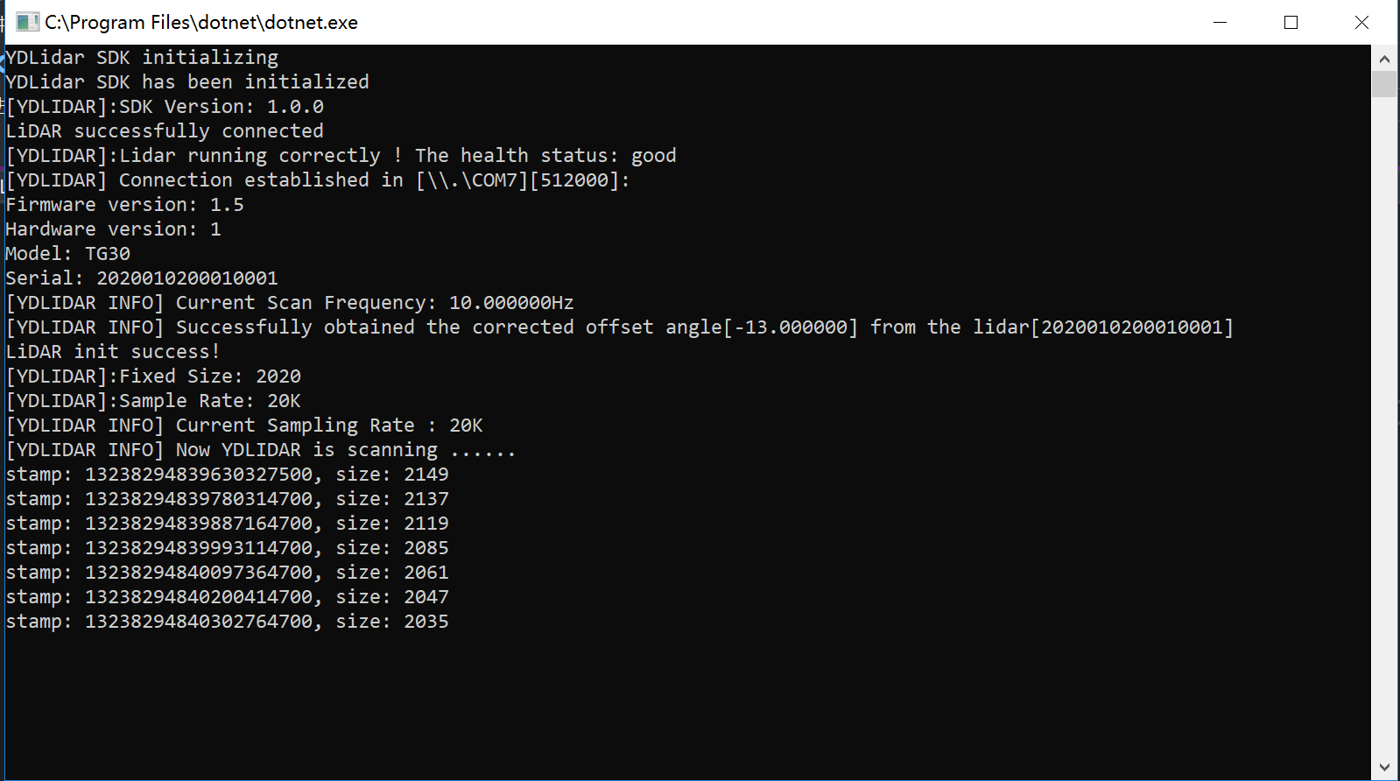
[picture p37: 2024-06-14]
f1tenth_ws/install/ydlidar_sdk/share/YDLIDAR_SDK/doc/howto/images/csharp_running.png

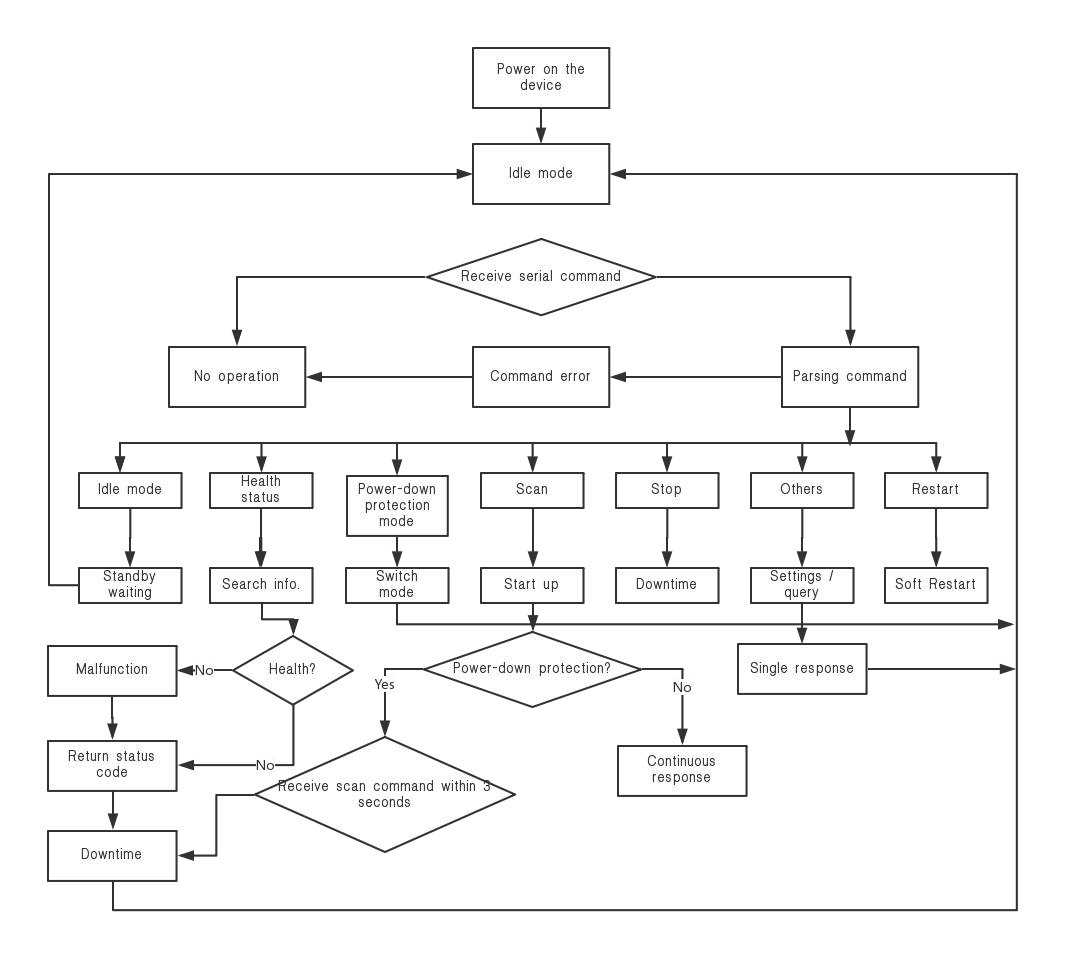
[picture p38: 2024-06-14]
f1tenth_ws/install/ydlidar_sdk/share/YDLIDAR_SDK/doc/images/system_workflow.png

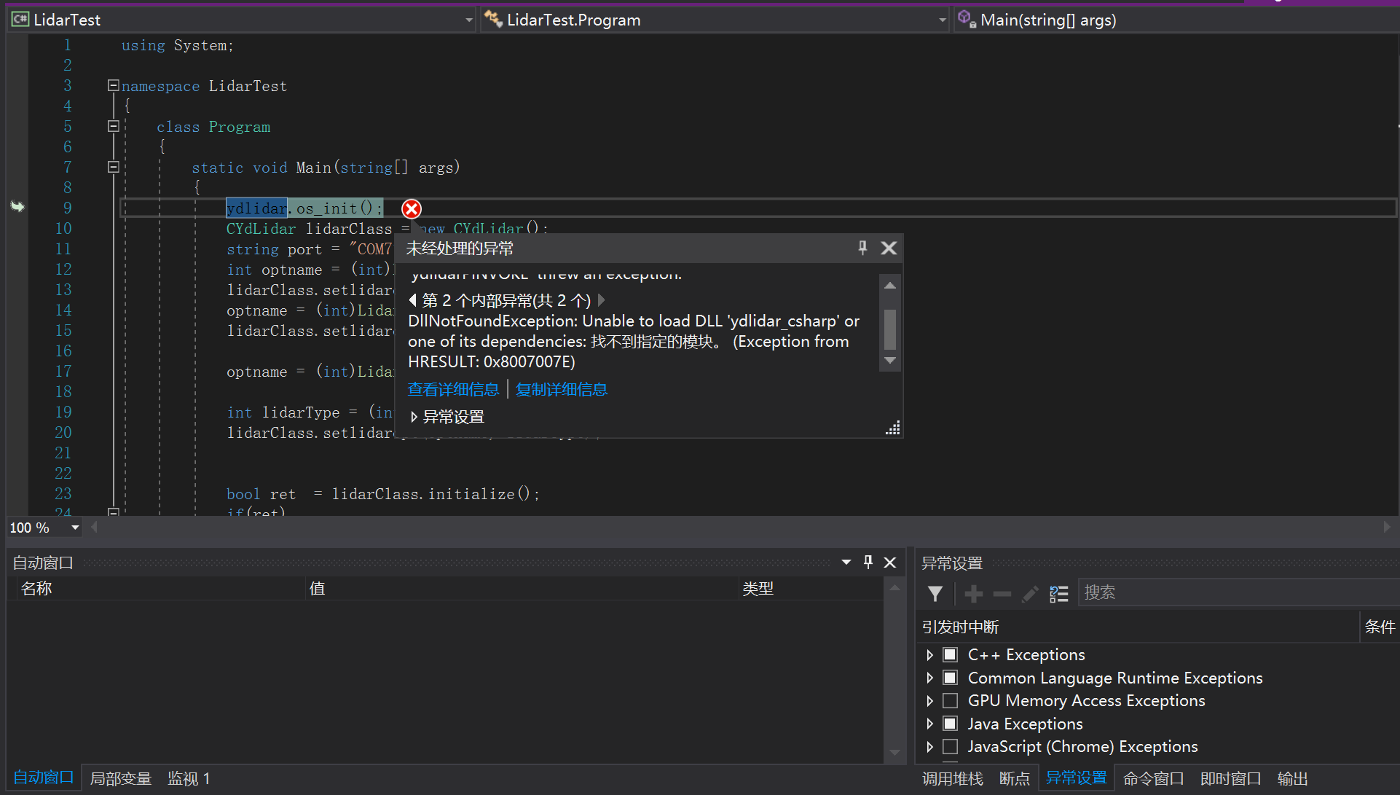
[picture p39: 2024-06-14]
f1tenth_ws/install/ydlidar_sdk/share/YDLIDAR_SDK/doc/howto/images/csharp_exception.png

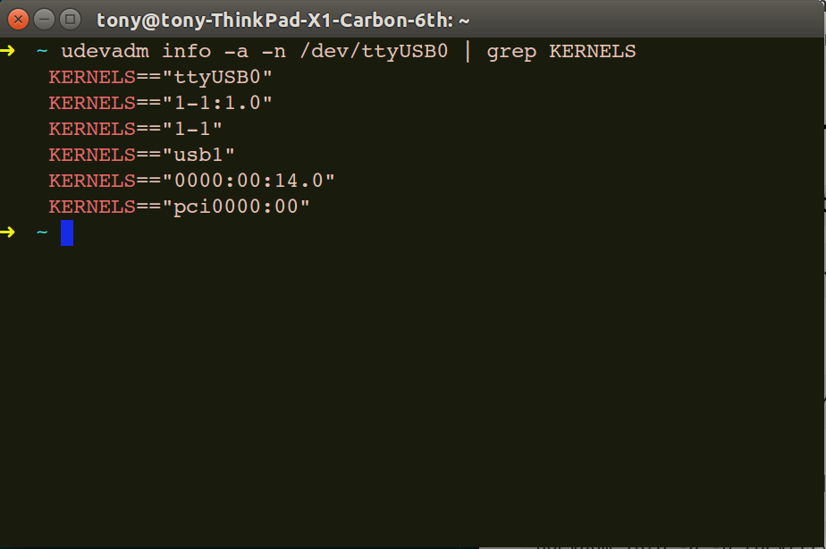
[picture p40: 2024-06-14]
f1tenth_ws/install/ydlidar_sdk/share/YDLIDAR_SDK/doc/howto/images/ttyUSB0.png

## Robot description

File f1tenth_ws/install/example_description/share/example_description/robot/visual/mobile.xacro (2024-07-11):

<?xml version='1.0' encoding='utf-8'?>
<robot xmlns:xacro="http://www.ros.org/wiki/xacro">
    
    <xacro:macro name="base_visual" params="">
        <visual>
            <origin xyz="${BASE_VISUAL['position']}" rpy="${BASE_VISUAL['orientation']}"/>
            <geometry>
                <!--mesh filename="file://$(find ${description_pkg})/meshes/link_0.stl"/-->
                <box size="${BASE_VISUAL['size']}"/>
            </geometry>
            <material name="link_color">
                <color rgba="${BASE_VISUAL['color']}"/>
            </material>
        </visual>
    </xacro:macro>


    <!-- Pure Visual (No dynamics) -->
    <xacro:macro name="manipulator_visual" params="">
        <link name="base_footprint">
            <origin xyz="0 0 0" rpy="0 0 0"/>
        </link>

        <link name="base_link">
            <origin xyz="0 0 0" rpy="0 0 0"/>
        </link>
        
        <link name="left_wheel"/>
        <link name="right_wheel"/>

        <link name="imu">
            <origin xyz="0 0 0" rpy="0 0 0"/>
        </link>

        <link name="steer">
            <origin xyz="0 0 0" rpy="0 0 0"/>
        </link>

        <link name="laser_frame">
            <origin xyz="0 0 0" rpy="0 0 0"/>
        </link>

        <link name="optical_odom">
            <origin xyz="0 0 0" rpy="0 0 0"/>
        </link>

        <joint name="base_link" type="fixed">
            <parent link="base_footprint"/>
            <child link="base_link"/>
            <origin xyz="0 0 0.03" rpy="0 0 0"/>
        </joint>

        <joint name="optical_odom" type="fixed">
            <parent link="base_link"/>
            <child link="optical_odom"/>
            <origin xyz="-0.043 0 0.0" rpy="0 0 3.14159"/>
        </joint>

        <!-- <link name="end_effector"/> -->

        <!-- <joint name="base_offset" type="fixed">
            <parent link="odom"/>
            <child link="base_link"/>
            <origin xyz="0 0 0" rpy="0 0 0"/>
        </joint> -->

        <joint name="left_wheel" type="revolute">
            <parent link="base_link"/>
            <child link="left_wheel"/>
            <origin xyz="0 0.0765 0" rpy="0 0 -0.0455"/>
            <axis xyz="0 1 0"/>
            <limit lower="-3.1459" upper="3.1459" velocity="1000.0" effort="1000.0"/>
        </joint>

        <joint name="right_wheel" type="revolute">
            <parent link="base_link"/>
            <child link="right_wheel"/>
            <origin xyz="0 -0.0765 0" rpy="0 0 0.0455"/>
            <axis xyz="0 1 0"/>
            <limit lower="-3.1459" upper="3.1459" velocity="1000.0" effort="1000.0"/>
        </joint>

        <joint name="imu" type="fixed">
            <parent link="base_link"/>
            <child link="imu"/>
            <origin xyz="0 0 0.09" rpy="0 0 -1.5729"/>
        </joint>

        <joint name="steer" type="revolute">
            <parent link="base_link"/>
            <child link="steer"/>
            <origin xyz="0.255 0 0" rpy="0 0 0"/>
            <axis xyz="0 0 1"/>
            <limit lower="-3.1459" upper="3.1459" velocity="1000.0" effort="1000.0"/>
        </joint>

        <joint name="laser_frame" type="fixed">
            <parent link="base_link"/>
            <child link="laser_frame"/>
            <origin xyz="0.255 0 0.09" rpy="0 0 0"/>
            <!-- <origin xyz="0.255 0 0" rpy="3.1416 0 0"/> -->
        </joint>

    </xacro:macro>
</robot>

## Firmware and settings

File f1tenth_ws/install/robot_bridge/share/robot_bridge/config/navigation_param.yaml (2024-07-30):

amcl:
  ros__parameters:

    # AMCL
    # alpha1: 0.004 #0.2
    # alpha2: 0.04 #0.2
    # alpha3: 0.008 #0.2
    # alpha4: 0.025 #0.2
    # alpha5: 0.2 
    # pf_err: 0.1 #0.05
    # pf_z: 0.5
    # laser_likelihood_max_dist: 2.0 #1.0
    # sigma_hit: 0.2 #0.2
    # z_hit: 0.5 #0.5
    # z_rand: 0.5

    # ODOM
    alpha1: 0.001 #0.005 #0.2
    alpha2: 0.001 #0.005 #0.2
    alpha3: 0.001 #0.005 #0.2
    alpha4: 0.001 #0.005 #0.2
    alpha5: 0.2 #0.2 
    pf_err: 0.2 #0.01 #0.05
    pf_z: 0.99 #0.99
    laser_likelihood_max_dist: 4.0 #4.0 #1.0
    sigma_hit: 0.1 #0.1 #0.2
    z_hit: 0.9 #0.9 #0.5
    z_rand: 0.5 #0.5

    always_reset_initial_pose: false
    base_frame_id: base_footprint
    beam_skip_distance: 0.5
    beam_skip_error_threshold: 0.9
    beam_skip_threshold: 0.3
    do_beamskip: false
    first_map_only: true
    global_frame_id: map
    initial_pose.x: 0.0
    initial_pose.y: 0.0
    initial_pose.yaw: 0.0
    initial_pose.z: 0.0
    lambda_short: 0.1
    laser_max_range: 12.0
    laser_min_range: -1.0
    laser_model_type: likelihood_field
    map_topic: map
    max_beams: 60
    max_particles: 2000 #2000
    min_particles: 500
    odom_frame_id: odom
    z_short: 0.05
    z_max: 0.05
    
    qos_overrides./tf.publisher.depth: 100
    qos_overrides./tf.publisher.durability: volatile
    qos_overrides./tf.publisher.history: keep_last
    qos_overrides./tf.publisher.reliability: reliable
    recovery_alpha_fast: 0.0
    recovery_alpha_slow: 0.0
    resample_interval: 1
    robot_model_type: nav2_amcl::DifferentialMotionModel
    save_pose_rate: 0.5
    scan_topic: scan
    set_initial_pose: true
    tf_broadcast: true
    transform_tolerance: 1.0
    update_min_a: 0.05
    update_min_d: 0.01
    use_sim_time: False

bt_navigator:
  ros__parameters:
    use_sim_time: False
    global_frame: map
    robot_base_frame: base_link
    odom_topic: /odom
    bt_loop_duration: 10
    default_server_timeout: 20
    # 'default_nav_through_poses_bt_xml' and 'default_nav_to_pose_bt_xml' are use defaults:
    # nav2_bt_navigator/navigate_to_pose_w_replanning_and_recovery.xml
    # nav2_bt_navigator/navigate_through_poses_w_replanning_and_recovery.xml
    # They can be set here or via a RewrittenYaml remap from a parent launch file to Nav2.
    plugin_lib_names:
    - nav2_compute_path_to_pose_action_bt_node
    - nav2_compute_path_through_poses_action_bt_node
    - nav2_smooth_path_action_bt_node
    - nav2_follow_path_action_bt_node
    - nav2_spin_action_bt_node
    - nav2_wait_action_bt_node
    - nav2_back_up_action_bt_node
    - nav2_drive_on_heading_bt_node
    - nav2_clear_costmap_service_bt_node
    - nav2_is_stuck_condition_bt_node
    - nav2_goal_reached_condition_bt_node
    - nav2_goal_updated_condition_bt_node
    - nav2_globally_updated_goal_condition_bt_node
    - nav2_is_path_valid_condition_bt_node
    - nav2_initial_pose_received_condition_bt_node
    - nav2_reinitialize_global_localization_service_bt_node
    - nav2_rate_controller_bt_node
    - nav2_distance_controller_bt_node
    - nav2_speed_controller_bt_node
    - nav2_truncate_path_action_bt_node
    - nav2_truncate_path_local_action_bt_node
    - nav2_goal_updater_node_bt_node
    - nav2_recovery_node_bt_node
    - nav2_pipeline_sequence_bt_node
    - nav2_round_robin_node_bt_node
    - nav2_transform_available_condition_bt_node
    - nav2_time_expired_condition_bt_node
    - nav2_path_expiring_timer_condition
    - nav2_distance_traveled_condition_bt_node
    - nav2_single_trigger_bt_node
    - nav2_goal_updated_controller_bt_node
    - nav2_is_battery_low_condition_bt_node
    - nav2_navigate_through_poses_action_bt_node
    - nav2_navigate_to_pose_action_bt_node
    - nav2_remove_passed_goals_action_bt_node
    - nav2_planner_selector_bt_node
    - nav2_controller_selector_bt_node
    - nav2_goal_checker_selector_bt_node
    - nav2_controller_cancel_bt_node
    - nav2_path_longer_on_approach_bt_node
    - nav2_wait_cancel_bt_node
    - nav2_spin_cancel_bt_node
    - nav2_back_up_cancel_bt_node
    - nav2_drive_on_heading_cancel_bt_node

bt_navigator_navigate_through_poses_rclcpp_node:
  ros__parameters:
    use_sim_time: False

bt_navigator_navigate_to_pose_rclcpp_node:
  ros__parameters:
    use_sim_time: False
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

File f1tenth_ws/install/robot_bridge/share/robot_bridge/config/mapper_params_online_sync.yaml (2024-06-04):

# Reference: https://github.com/SteveMacenski/slam_toolbox/blob/foxy-devel/config/mapper_params_online_async.yaml

sync_slam_toolbox_node:
  ros__parameters:

    # Plugin params
    solver_plugin: solver_plugins::CeresSolver
    ceres_linear_solver: SPARSE_NORMAL_CHOLESKY
    ceres_preconditioner: SCHUR_JACOBI
    ceres_trust_strategy: LEVENBERG_MARQUARDT
    ceres_dogleg_type: TRADITIONAL_DOGLEG
    ceres_loss_function: None

    # ROS Parameters
    odom_frame: odom
    map_frame: map
    base_frame: base_footprint
    scan_topic: /scan
    mode: mapping #localization

    # if you'd like to immediately start continuing a map at a given pose
    # or at the dock, but they are mutually exclusive, if pose is given
    # will use pose
    #map_file_name: test_steve
    #map_start_pose: [0.0, 0.0, 0.0]
    #map_start_at_dock: true

    debug_logging: false
    throttle_scans: 2
    transform_publish_period: 0.02 #if 0 never publishes odometry
    map_update_interval: 5.0
    resolution: 0.05
    max_laser_range: 12.0 #for rastering images
    minimum_time_interval: 0.5
    transform_timeout: 0.2
    tf_buffer_duration: 30.
    stack_size_to_use: 9000000000 #// program needs a larger stack size to serialize large maps
    enable_interactive_mode: true

    # General Parameters
    use_scan_matching: true
    use_scan_barycenter: true
    minimum_travel_distance: 0.5
    minimum_travel_heading: 0.5
    scan_buffer_size: 10
    scan_buffer_maximum_scan_distance: 10.0
    link_match_minimum_response_fine: 0.1  
    link_scan_maximum_distance: 1.5
    loop_search_maximum_distance: 3.0
    do_loop_closing: true 
    loop_match_minimum_chain_size: 10           
    loop_match_maximum_variance_coarse: 3.0  
    loop_match_minimum_response_coarse: 0.35    
    loop_match_minimum_response_fine: 0.45

    # Correlation Parameters - Correlation Parameters
    correlation_search_space_dimension: 0.5
    correlation_search_space_resolution: 0.01
    correlation_search_space_smear_deviation: 0.1 

    # Correlation Parameters - Loop Closure Parameters
    loop_search_space_dimension: 8.0
    loop_search_space_resolution: 0.05
    loop_search_space_smear_deviation: 0.03

    # Scan Matcher Parameters
    distance_variance_penalty: 0.5      
    angle_variance_penalty: 1.0    

    fine_search_angle_offset: 0.00349     
    coarse_search_angle_offset: 0.349   
    coarse_angle_resolution: 0.0349        
    minimum_angle_penalty: 0.9
    minimum_distance_penalty: 0.5
    use_response_expansion: true

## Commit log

2024-06-04 Nav2 Navigation
    [body.gazebo.xacro, common.xacro, diff_drive_controller.yaml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]
2024-06-04 add ydlidar and robot localization
    [test_ros_robot_localization_listener.yaml]
2024-07-04 Before Tuning AMCL
    [end_effector.stl, lidar0.csv, lidar1.csv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]
2024-07-11 Update ros bag for ekf
    [mobile.xacro]
2024-07-11 optical odom tf
    [sensor_calibration.yaml]
2024-07-18 Add Docker
    [end_effector.stl, lidar0.csv, lidar1.csv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]
2024-07-24 Update src
    [sensor_calibration.yaml]
2024-07-30 Update src (Final Internship)
    [test_ros_robot_localization_listener.yaml]
2024-07-30 Update README.md correct equation odometry
2024-10-25 edit docker compose for connect joystick
    [end_effector.stl, link_1.stl, link_2.stl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]
2024-10-30 add t265_odom
    tf to base_footprint
    calibrate
